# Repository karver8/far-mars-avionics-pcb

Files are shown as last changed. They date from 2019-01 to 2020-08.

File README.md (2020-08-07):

# far-mars-avionics-controller

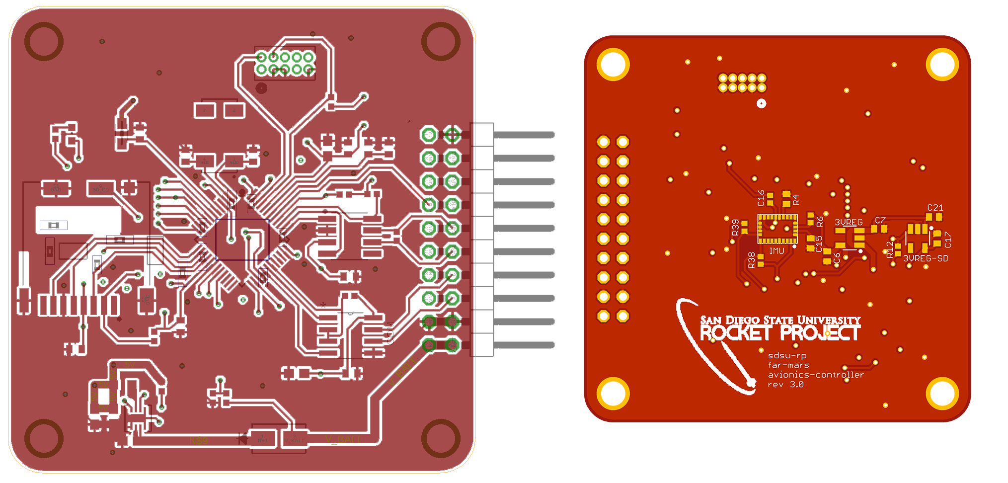
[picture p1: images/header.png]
PCB Layout Graphic


The **far-mars-avionics-controller** is a custom built printed circuit board that performs data aquisition, logging, and communication, all in one highly power effecient, light weight, and compact design. This circuit was built around the FAR/MARS rocket competition, which challenges teams to design a LOX/Methane rocket to accuratley target an altitude of 45,000 feet.

### Features
* Dual(5V/3.3V) Supply ARM Cortex M0+ microcontroller
* 9 multi-purpose 5V I/O pins (+1 DIO PIN)
* Up to 9 12bit and 2 16bit Analog to Digital channels.
* RS-485 Transceiver for long distance LVDS ground communications
* CANbus Transceiver for future feature expansion(untested)
* BNO055 Inertial Measurement Unit
* Locking microSD card slot for secure, vibration resistant data logging
* 5-17V Input Range allowing for versatile power supply.
* Power Effecient enabling the use of a tiny battery
* Very light, weighs less than an ounce!
* Built-in battery charge monitoring.
* Highly accurate crystal for detailed timestamping.

### Firmware

The FAR/MARS rocket uses a FreeRTOS implementation to safley and predictabley manage the various avionics tasks required to launch the rocket. Documentation and development of the firmware for this board can be found in our [far-mars-onboard-firmware](https://github.com/SDSURocketProject/far-mars-onboard-firmware) repository. 

### Documentation
Here is everything you need to interface with this PCB and/or to write your own drivers and firmware:
* [Pinout](/documentation/pinout.pdf "Pinout")
* [Schematic](/documentation/schematic.pdf "Schematic")
* [Mechanical Drawing](/documentation/mech_drawing.pdf "Drawing")
* [Device Datasheet Collection](/documentation/Datasheets "Device Datasheet Collection")

### Assembly
It is highly recommend that you outsource the assembly of this PCB. This design has a lot of tiny surface mount components, on both sides of the board, so unless you have experience reflowing on two sides, this will be almost impossible to assemble yourself. We used MacroFab for the most recent version of this PCB. The current BOM is also optimized to take advantage of their 10-day turnaround service. Here is everything you need to assemble your own avionics controller:
* [Assembly Guide](/assembly#assembly-guide "Instructions")
* [Bill of Materials](/assembly/BOM#bill-of-materials "Bill of Materials")
* [Gerber Files](/assembly/Gerbers)
* [Design Slides](/assembly/Physical%20Summary.pdf "Physical Summary")
* **Schematic & Layout Files are in the top directory**

### Remarks
The far-mars-avionics-controller is entirley functional and usable on any system with similar requirements to the FAR/MARS Lady Elizabeth rocket. Furthermore the CANbus port included in the design, once tested, will also allow for the PCB to interface with virtually any existing CANbus compatible product/system(e.g. Motor Controllers, Thermocouple modules). 

That all said the main purpose of this project was to demonstrate SDSU Rocket Projects ability to design highly purpose built custom electronics, and it was specifically designed around the rules specified by the FAR/MARS rocket competition. This PCB is far from being an all in one solution to any Avionics requirments you may have. The design may find most of its value as a supplement to a larger system.

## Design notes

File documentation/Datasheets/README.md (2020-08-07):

### Datasheet Index
* [Atmel SAMC21G ARM Cortex M0](/documentation/Datasheets/atmel-samc21datasheet.pdf "Atmel SAMC21G ARM Cortex M0+")
* [BNO055 Inertial Measurment Unit](/documentation/Datasheets/BST-BNO055-DS000.pdf "BNO055 Inertial Measurment Unit")
* [SanDisk microSD](/documentation/Datasheets/sandisk-microSD.pdf "SanDisk microSD")
* [microSD Slot Mechanical Specs](/documentation/Datasheets/microSD_DM3_catalog.pdf "microSD Slot Mechanical Specs")
* [RS485 Transceiver](/documentation/Datasheets/sn65hvd35.pdf "RS485 Transciever ")
* [CAN Transceiver](/documentation/Datasheets/MCP2561T.pdf)
* [5V DC/DC Switching Regulator](/documentation/Datasheets/tps62161.pdf)
* [3.3V Linear Regulator](/documentation/Datasheets/tlv702.pdf)
* [Reverse Protection Diode](/documentation/Datasheets/ds13002.pdf)
* [Tuning Fork Crystal](/documentation/Datasheets/abs25.pdf)

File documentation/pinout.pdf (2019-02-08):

# FAR/MARS AVIONICS PINOUT

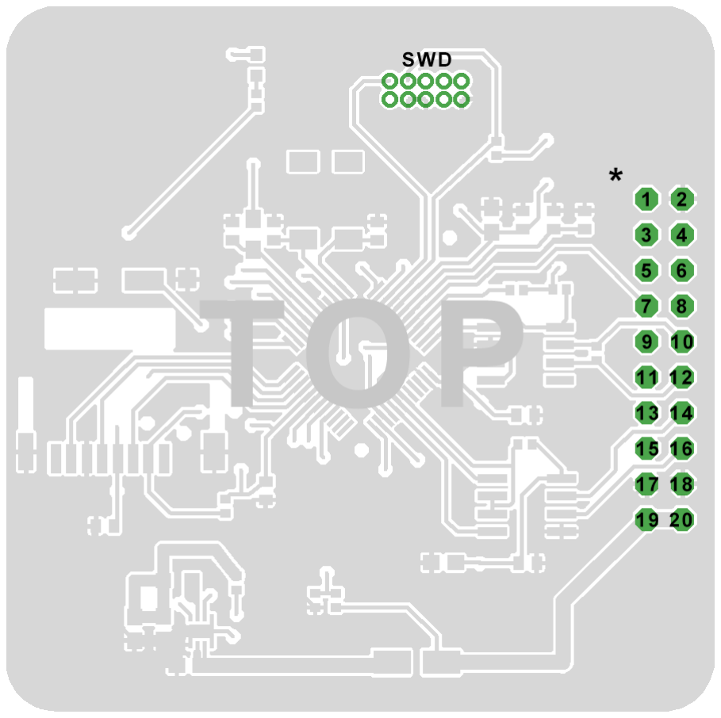
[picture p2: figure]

FULL PIN FUNCTION FOUND ON SAMC21G "I/O Multiplexing & Considerations", pg. 30 of Datasheet
Physical PIN # | Primary Function | SAMC21 PIN # | Supply | ADC | SD-ADC(16-bit) | PWM | SERCOM A | MISC
1 | 5V | -
2 | GND | -
3 | Multi-Function I/O | PB02 | 5V | AIN10 | | | SER5:0
4 | Multi-Function I/O | PB03 | 5V | AIN11 | | | SER5:1
5 | Multi-Function I/O | PA02 | 5V | AIN0 | | | | DAC
6 | Multi-Function I/O | PB08 | 5V | AIN2 | SDADC1:N | TC4:0 | SER4:0
7 | Digital I/O | PA28 | 5V
8 | Multi-Function I/O | PB09 | 5V | AIN3 | SDADC1:P | TC4:1 | SER4:1
9 | Multi-Function I/O | PA04 | 5V | AIN4 | | TC0:0 | SER0:0 | REFB
10 | CAN H | -
11 | Multi-Function I/O | PA05 | 5V | AIN5 | | TC0:1 | SER0:1
12 | CAN L | -
13 | Multi-Function I/O | PA06 | 5V | AIN6 | SDADC0:N | TC1:0 | SER0:2
14 | RS485 B | -
15 | Multi-Function I/O | PA07 | 5V | AIN7 | SDADC0:P | TC1:1 | SER0:3
16 | RS485 A | -
17 | GND | -
18 | GND | -
19 | VIN/BATT | -
20 | VIN/BATT | -

### Lady Elizabeth Specific

Physical PIN # | Primary Function | SAMC21 PIN # | Supply | Static Hot Fire | Launch | Description
1 | 5V | - | | UNUSED | UNUSED
2 | GND | - | | UNUSED | UNUSED
3 | 12 bit ADC | PB02 | 5V | TBD | UNUSED | TBD
4 | 12 bit ADC | PB03 | 5V | TBD | UNUSED | TBD
5 | 12 bit ADC | PA02 | 5V | Liquid Methane Tank PT | Liquid Methane Tank PT | 1500PSI 0.5-4.5V Analog PT
6 | 12 bit ADC | PB08 | 5V | Liquid Oxygen Tank PT | Liquid Oxygen Tank PT | 1500PSI 0.5-4.5V Analog PT
7 | Digital I/O | PA28 | 5V | UNUSED | UNUSED
8 | 16 bit SDADC | PB09 | 5V | Helium Tank PT | Helium Tank PT | 5800PSI 0-5V Analog PT
9 | Multi-Function I/O | PA04 | 5V | UNUSED | UNUSED
10 | CAN H | - | | UNUSED | UNUSED
11 | Multi-Function I/O | PA05 | 5V | UNUSED | UNUSED
12 | CAN L | - | | UNUSED | UNUSED
13 | 12 bit ADC | PA06 | 5V | TBD | UNUSED | TBD
14 | RS485 B | - | | Ground Coms | Ground Coms | Up to 1500m, Half-Duplex
15 | 16 bit SDADC | PA07 | 5V | Chamber Pressure PT | Chamber Pressure PT | TBD
16 | RS485 A | - | | Ground Coms | Ground Coms | Up to 1500m, Half-Duplex
17 | GND | - | | Ducer GND | Ducer GND | Ducer GND
18 | GND | - | | 11.1V 3S LiPo Ground | 11.1V 3S LiPo Ground | 11.1V 3S LiPo Ground
19 | VIN/BATT | - | | Ducer VOUT | Ducer VOUT | Ducer VOUT
20 | VIN/BATT | - | | 11.1V 3S LiPo Power In | 11.1V 3S LiPo Power In | 11.1V 3S LiPo Power In

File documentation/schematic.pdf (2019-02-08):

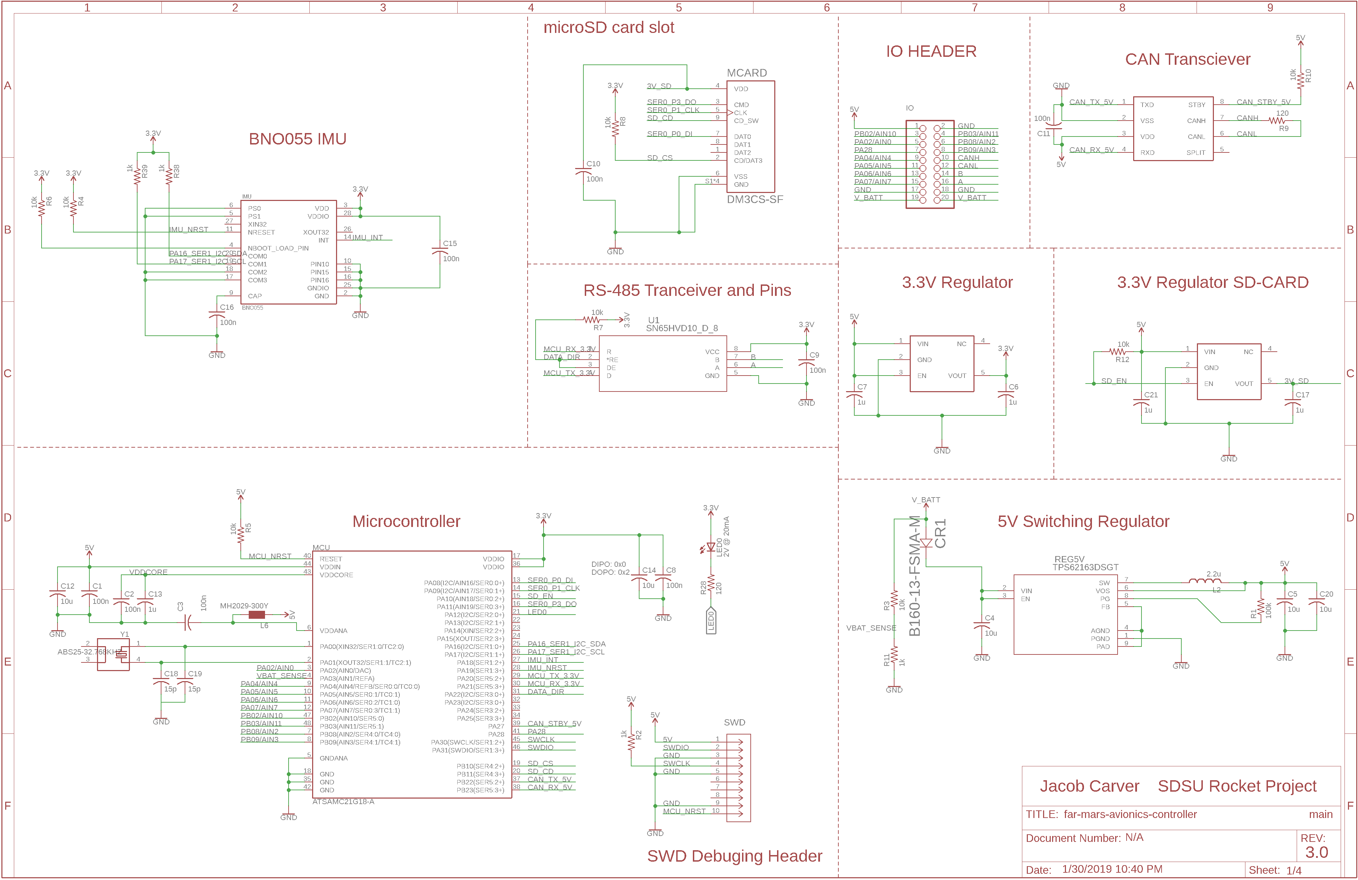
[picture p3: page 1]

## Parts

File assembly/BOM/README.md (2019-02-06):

## Bill of Materials

Here are two lists of materials you will need to both assemble and interface with the board.

* [Materials for PCB Assembly](https://github.com/SDSURocketProject/far-mars-avionics-pcb/blob/master/assembly/BOM/Onboard-BOM.csv)
* [Other Required Items](https://github.com/SDSURocketProject/far-mars-avionics-pcb/blob/master/assembly/BOM/OffBoard-BOM.csv)

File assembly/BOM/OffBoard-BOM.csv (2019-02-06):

Component/Part Name | Part Number | Link | Description | Vendor
Atmel ICE Debugger | ATATMEL-ICE-ND | https://www.digikey.com/product-detail/en/microchip-technology/ATATMEL-ICE/ATATMEL-ICE-ND/4753379 | PROGRAMMER FOR SAM | Digikey
Female Main Connector | A3DDH-2006G-ND | https://www.digikey.com/product-detail/en/te-connectivity-amp-connectors/A3DDH-2006G/A3DDH-2006G-ND/826121 | IDC CABLE - AKR20H/AE20G/AKR20H | Digikey
RS485 FTDI Wire End | USB-RS485-WE-1800-BT-FTDI_IT | https://www.amazon.com/FTDI-USB-RS485-WE-1800-BT-CABLE-RS485-SERIAL/dp/B00DK85QY4?s=electronics | RS485 to USB FTDI Adapter | Amazon
5-17V Power Source | N/A | N/A | N/A | Any

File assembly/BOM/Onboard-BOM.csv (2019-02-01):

Component/Part Name | Part Number | Link | Description | Vendor | MacroFab House Part | Qty Per Brd
ARM® Cortex®-M0+ SAM C21 | ATSAMC21G18A-AUTCT-ND | https://www.digikey.com/product-detail/en/microchip-technology/ATSAMC21G18A-AUT/ATSAMC21G18A-AUTCT-ND/5876003 | IC MCU 32BIT 256KB FLASH 48TQFP | Digikey |  | 1
10 (8 + 2) Position microSD Card Connector | HR1972CT-ND | https://www.digikey.com/product-detail/en/hirose-electric-co-ltd/DM3CS-SF/HR1972CT-ND/2602740 | CONN MICRO SD CARD HINGED TYPE | Digikey |  | 1
Red 633nm LED | 475-2512-1-ND | https://www.digikey.com/product-detail/en/osram-opto-semiconductors-inc/LS-Q976-NR-1/475-2512-1-ND/1802639 | LED RED DIFFUSED 0603 SMD | Digikey |  | 1
Ferrite Bead Filter | MH2029-300YCT-ND | https://www.digikey.com/product-detail/en/bourns-inc/MH2029-300Y/MH2029-300YCT-ND/3741761 | FERRITE BEAD 30 OHM 0805 1LN | Digikey |  | 1
2.2µH Unshielded Wirewound Inductor | 587-2064-1-ND | https://www.digikey.com/product-detail/en/taiyo-yuden/BRL2012T2R2M/587-2064-1-ND/1789011 | FIXED IND 2.2UH 550MA 390 MOHM | Digikey |  | 1
Right Angle 20 position Main Header | A97487-ND | https://www.digikey.com/product-detail/en/te-connectivity-amp-connectors/5103311-5/A97487-ND/1596774 | CONN HEADER R/A 20POS 2.54MM | Digikey |  | 1
BNO055 Inertial Measurment Unit | 828-1058-1-ND | https://www.digikey.com/product-detail/en/bosch-sensortec/BNO055/828-1058-1-ND/6136309 | IMU ACCEL/GYRO/MAG I2C 28LGA | Digikey |  | 1
Diode Schottky Reverse Voltage Protection | B140-FDICT-ND | https://www.digikey.com/product-detail/en/diodes-incorporated/B140-13-F/B140-FDICT-ND/815319 | DIODE SCHOTTKY 40V 1A SMA | Digikey | Yes | 1
10µF Ceramic Capacitor | 445-9065-1-ND | https://www.digikey.com/product-detail/en/tdk-corporation/C1608X5R1C106M080AB/445-9065-1-ND/3648729 | CAP CER 10UF 16V X5R 0603 | Digikey | Yes | 5
0.1µF Ceramic Capacitor | 490-3261-1-ND | https://www.digikey.com/product-detail/en/murata-electronics-north-america/GRM155R71C104KA88D/490-3261-1-ND/702802 | CAP CER 0.1UF 16V X7R 0402 | Digikey | Yes | 9
3.3V Linear Voltage Regulator | 296-32415-1-ND | https://www.digikey.com/product-detail/en/texas-instruments/TLV70233DBVR/296-32415-1-ND/3505572 | IC REG LINEAR 3.3V 300MA SOT23-5 | Digikey | Yes | 2
1µF Ceramic Capacitor | 445-4978-1-ND | https://www.digikey.com/product-detail/en/tdk-corporation/C1005X5R1C105K050BC/445-4978-1-ND/2093592 | CAP CER 1UF 16V X5R 0402 | Digikey | Yes | 5
15pF Capacitor for Crystal | 478-1072-1-ND | https://www.digikey.com/product-detail/en/avx-corporation/04025A150JAT2A/478-1072-1-ND/564104 | CAP CER 15PF 50V C0G/NP0 0402 | Digikey |  | 2
CANbus Transciever | MCP2561T-E/SNCT-ND | https://www.digikey.com/product-detail/en/microchip-technology/MCP2561T-E-SN/MCP2561T-E-SNCT-ND/5148846 | IC TXRX CAN 8SOIC | Digikey |  | 1
10k Chip Resistor | P10KJCT-ND | https://www.digikey.com/product-detail/en/microchip-technology/MCP2561T-E-SN/MCP2561T-E-SNCT-ND/5148846 | RES SMD 10K OHM 5% 1/10W 0402 | Digikey | Yes | 8
1k Chip Resistor | P1.0KJCT-ND | https://www.digikey.com/product-detail/en/panasonic-electronic-components/ERJ-2GEJ102X/P1.0KJCT-ND/146897 | RES SMD 1K OHM 5% 1/10W 0402 | Digikey | Yes | 4
100k Chip Resistor | P100KJCT-ND | https://www.digikey.com/product-detail/en/panasonic-electronic-components/ERJ-2GEJ104X/P100KJCT-ND/146730 | RES SMD 100K OHM 5% 1/10W 0402 | Digikey | Yes | 1
CAN Termination Resistor | ERJ-S02F1200X-ND | https://www.digikey.com/product-detail/en/panasonic-electronic-components/ERJ-S02F1200X/ERJ-S02F1200X-ND/672934 | RES SMD 120 OHM 1% 1/10W 0402 | Digikey |  | 2
5V Switch Regulator | 296-30228-1-ND | https://www.digikey.com/product-detail/en/texas-instruments/TPS62163DSGT/296-30228-1-ND/2982147 | IC REG BUCK 5V 1A SYNC 8WSON | Digikey |  | 1
SWD Header | 609-3712-ND | https://www.digikey.com/product-detail/en/amphenol-icc-fci/20021111-00010T4LF/609-3712-ND/2209072 | CONN HEADER VERT 10POS 1.27MM | Digikey |  | 1
RS485 Transciever | 296-24734-1-ND | https://www.digikey.com/product-detail/en/texas-instruments/SN65HVD10MDREP/296-24734-1-ND/2092556 | IC TXRX RS485 EP 3.3V 8SOIC | Digikey |  | 1
32.768kHz ±10ppm Crystal | 535-9809-1-ND | https://www.digikey.com/product-detail/en/abracon-llc/ABS25-32.768KHZ-1-T/535-9809-1-ND/2001432 | CRYSTAL 32.7680KHZ 12.5PF SMD | Digikey |  | 1

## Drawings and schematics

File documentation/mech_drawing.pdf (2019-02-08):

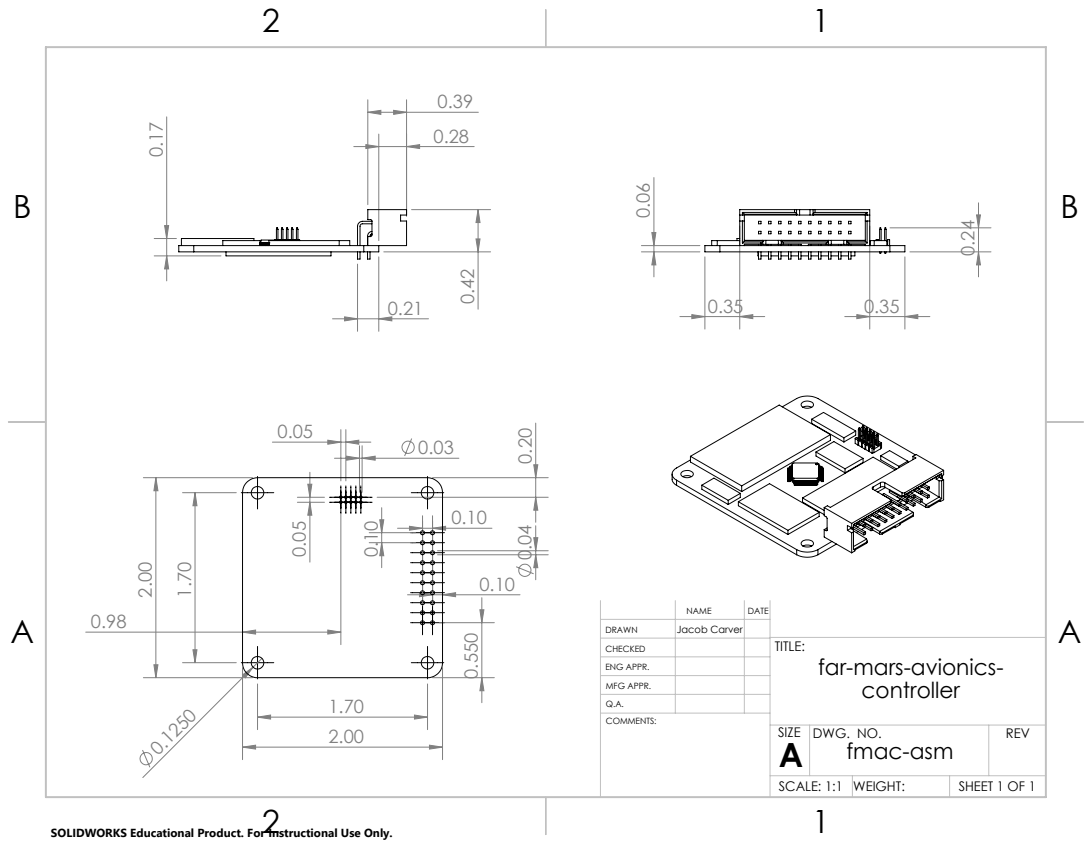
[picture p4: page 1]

DRAWN | Jacob Carver
CHECKED | | TITLE: far-mars-avionics-controller

ENG APPR.
MFG APPR.
Q.A.

SIZE A | DWG. NO. fmac-asm | REV

SCALE: 1:1 | WEIGHT: | SHEET 1 OF 1

SOLIDWORKS Educational Product. For Instructional Use Only.

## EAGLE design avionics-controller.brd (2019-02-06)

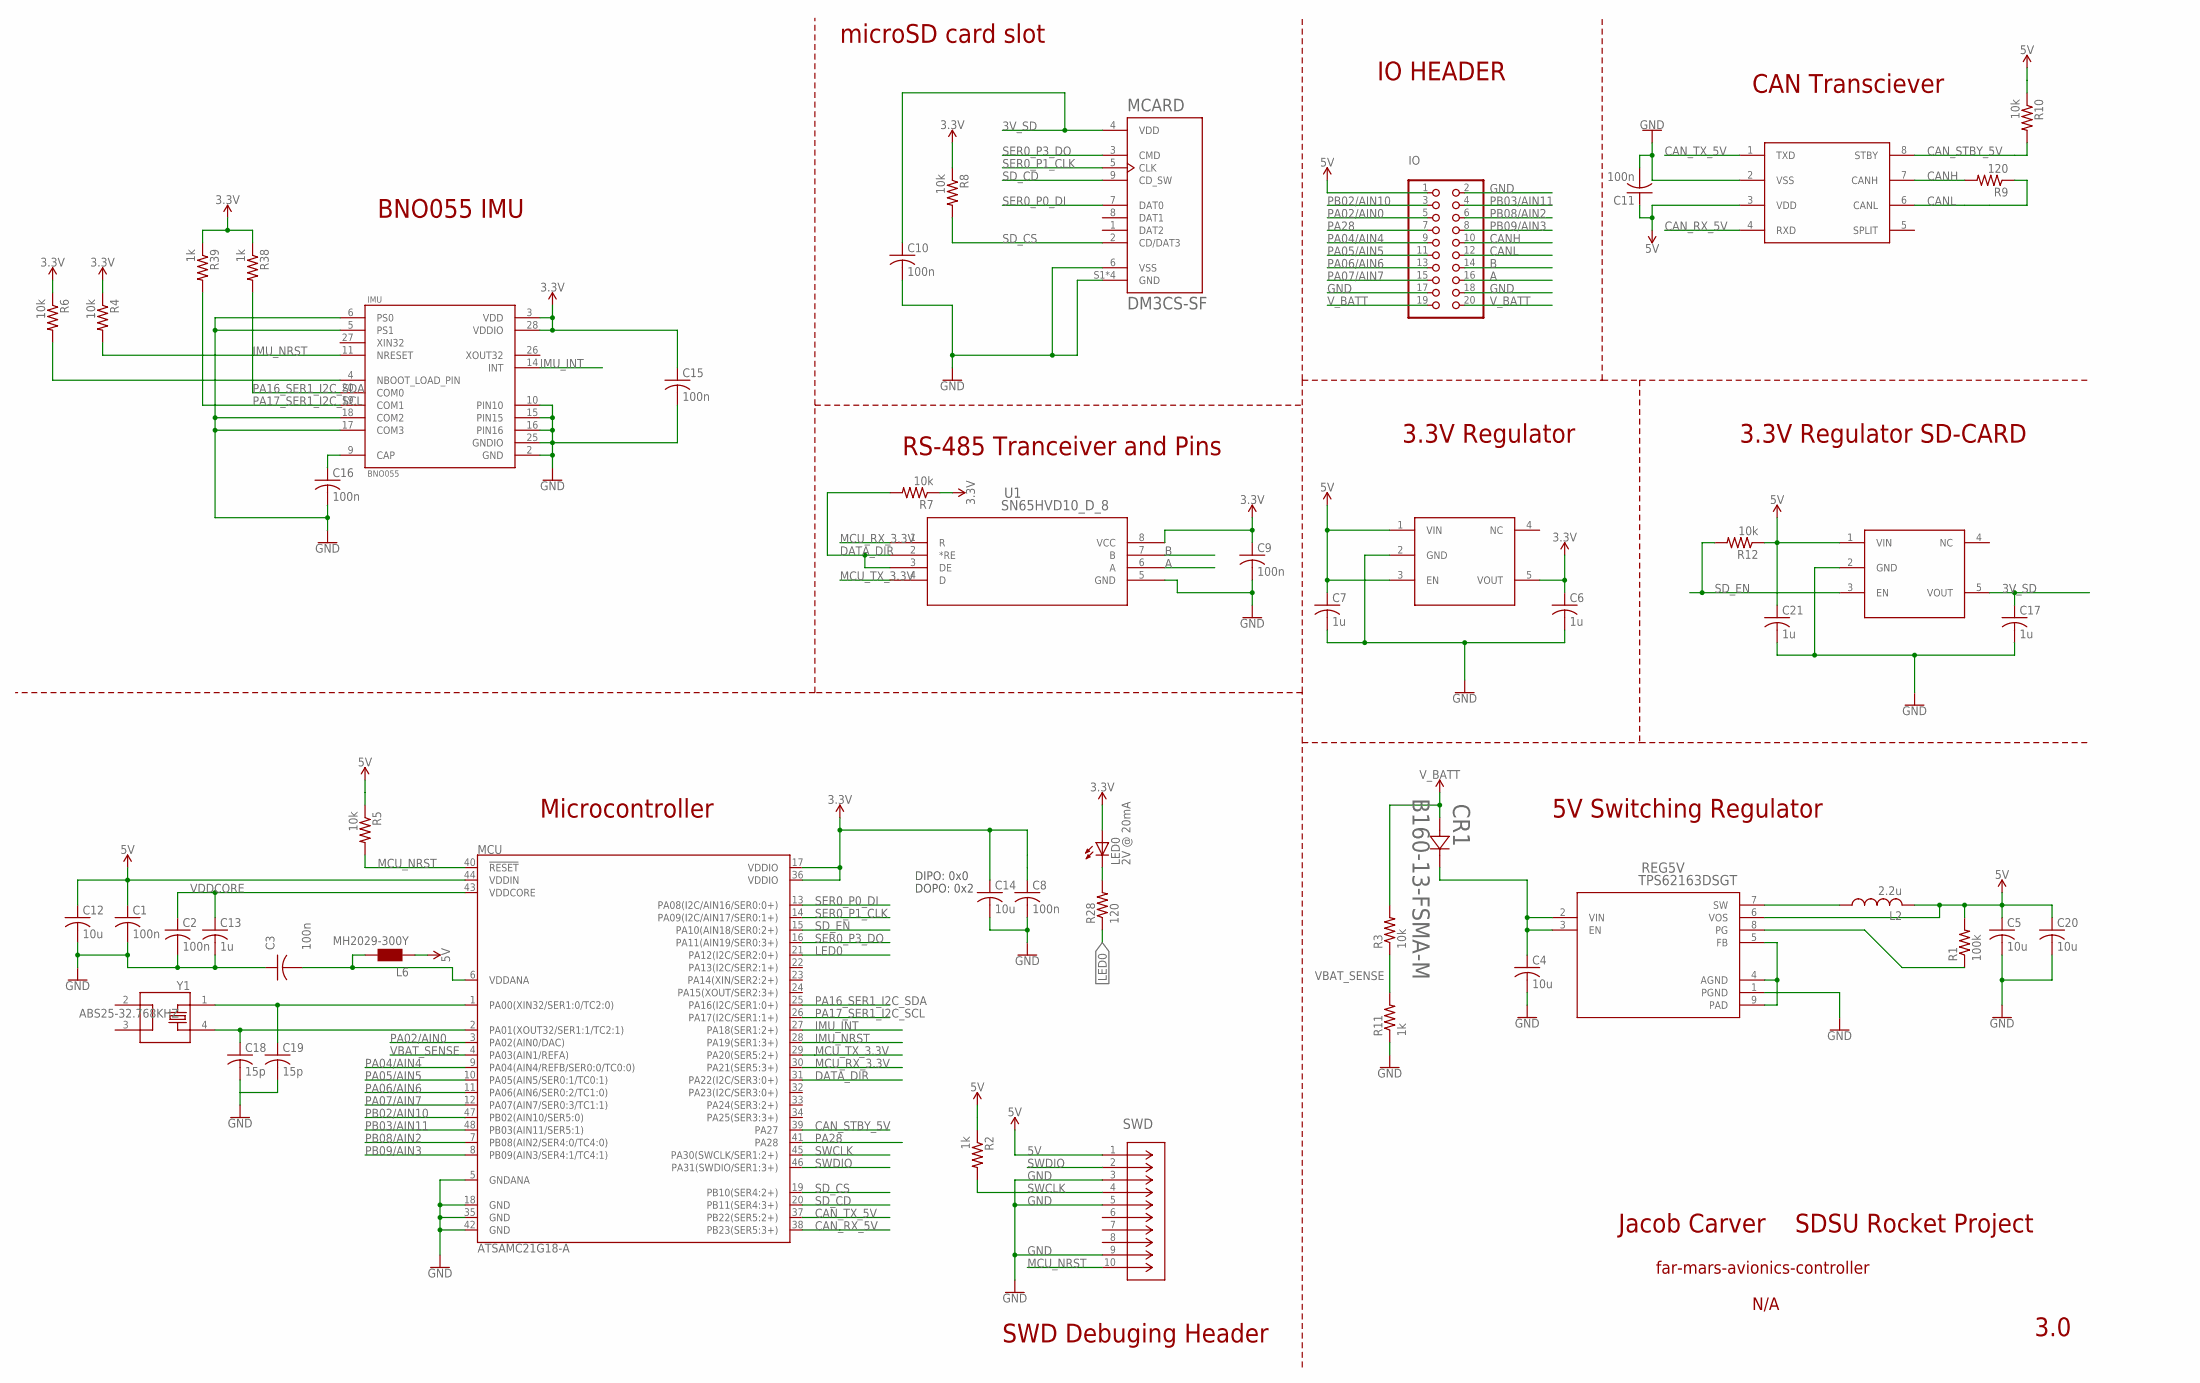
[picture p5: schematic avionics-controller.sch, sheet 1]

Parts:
3VREG, 3VREG-SD: 3.3VREGULATOR; SOT95P280X110-5
C1, C2, C3, C8, C9, C10, C11, C15, C16: 100n; C0402
C4, C5, C12, C14, C20: 10u; C0603
C6, C7, C13, C17, C21: 1u; C0402
C18, C19: 15p; C0402
CAN: MCP2561T-E8SOIC; SOIC127P600X175-8
CR1: B160-13-FSMA-M; SMA-M
IMU: BNO055; LGA28R50P4X10_380X520X100
IO: PINHD-2X10/90; 2X10/90
L2: 2.2u; L2012C
L6: MH2029-300Y; 0805
LED0: 2V @ 20mA; CHIPLED_0603
MCARD: DM3CS-SF; HRS_DM3CS-SF
MCU: ATSAMC21G18-A; TQFP-48
R1: 100k; R0402
R2, R11, R38, R39: 1k; R0402
R3, R4, R5, R6, R7, R8, R10, R12: 10k; R0402
R9, R28: 120; R0402
REG5V: TPS62163DSGT; DSG8_1P6X0P9
SWD: DEBUG-HEADER; CONN_MINITEK_2X5_HDR
U1: SN65HVD10_D_8; D8
Y1: ABS25-32.768KHZ; ABS25-32.768KHZ-6-T

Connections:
3.3V: 3VREG.5 (VOUT), C6.1, C8.1, C9.1, C14.1, C15.1, IMU.3 (VDD), IMU.28 (VDDIO), LED0.A, MCU.17 (VDDIO), MCU.36 (VDDIO), R4.1, R6.1, R7.1, R8.1, R38.1, R39.1, U1.8 (VCC)
3V_SD: 3VREG-SD.5 (VOUT), C10.1, C17.1, MCARD.4 (VDD)
5V: 3VREG.1 (VIN), 3VREG.3 (EN), 3VREG-SD.1 (VIN), C1.1, C5.1, C7.1, C11.1, C12.1, C20.1, C21.1, CAN.3 (VDD), IO.1, L2.2, L6.1, MCU.44 (VDDIN), R1.2, R2.1, R5.1, R10.1, R12.1, REG5V.6 (VOS), SWD.1
A: IO.16, U1.6 (A)
B: IO.14, U1.7 (B)
CANH: CAN.7 (CANH), IO.10, R9.2
CANL: CAN.6 (CANL), IO.12, R9.1
CAN_RX_5V: CAN.4 (RXD), MCU.38 (PB23(SER5:3+))
CAN_STBY_5V: CAN.8 (STBY), MCU.39 (PA27), R10.2
CAN_TX_5V: CAN.1 (TXD), MCU.37 (PB22(SER5:2+))
DATA_DIR: MCU.31 (PA22(I2C/SER3:0+)), R7.2, U1.2 (*RE), U1.3 (DE)
GND: 3VREG.2 (GND), 3VREG-SD.2 (GND), C1.2, C2.2, C3.1, C4.2, C5.2, C6.2, C7.2, C8.2, C9.2, C10.2, C11.2, C12.2, C13.2, C14.2, C15.2, C16.2, C17.2, C18.2, C19.2, C20.2, C21.2, CAN.2 (VSS), IMU.2 (GND), IMU.5 (PS1), IMU.6 (PS0), IMU.10 (PIN10), IMU.15 (PIN15), IMU.16 (PIN16), IMU.17 (COM3), IMU.18 (COM2), IMU.25 (GNDIO), IO.2, IO.17, IO.18, MCARD.6 (VSS), MCARD.S1 (GND), MCARD.S2 (GND), MCARD.S3 (GND), MCARD.S5 (GND), MCU.5 (GNDANA), MCU.18 (GND), MCU.35 (GND), MCU.42 (GND), R11.1, REG5V.1 (PGND), SWD.3, SWD.5, SWD.9, U1.5 (GND)
IMU_INT: IMU.14 (INT), MCU.27 (PA18(SER1:2+))
IMU_NRST: IMU.11 (NRESET), MCU.28 (PA19(SER1:3+)), R4.2
LED0: MCU.21 (PA12(I2C/SER2:0+)), R28.1
MCU_NRST: MCU.40 (!RESET!), R5.2, SWD.10
MCU_RX_3.3V: MCU.30 (PA21(SER5:3+)), U1.1 (R)
MCU_TX_3.3V: MCU.29 (PA20(SER5:2+)), U1.4 (D)
unnamed: R1.1, REG5V.8 (PG)
unnamed: C3.2, L6.2, MCU.6 (VDDANA)
unnamed: L2.1, REG5V.7 (SW)
unnamed: REG5V.4 (AGND), REG5V.5 (FB), REG5V.9 (PAD)
unnamed: C4.1, CR1.1 (12), REG5V.2 (VIN), REG5V.3 (EN)
unnamed: C19.1, MCU.1 (PA00(XIN32/SER1:0/TC2:0)), Y1.1
unnamed: C18.1, MCU.2 (PA01(XOUT32/SER1:1/TC2:1)), Y1.4
unnamed: C16.1, IMU.9 (CAP)
unnamed: IMU.4 (NBOOT_LOAD_PIN), R6.2
unnamed: LED0.C, R28.2
PA02/AIN0: IO.5, MCU.3 (PA02(AIN0/DAC))
PA04/AIN4: IO.9, MCU.9 (PA04(AIN4/REFB/SER0:0/TC0:0))
PA05/AIN5: IO.11, MCU.10 (PA05(AIN5/SER0:1/TC0:1))
PA06/AIN6: IO.13, MCU.11 (PA06(AIN6/SER0:2/TC1:0))
PA07/AIN7: IO.15, MCU.12 (PA07(AIN7/SER0:3/TC1:1))
PA16_SER1_I2C_SDA: IMU.20 (COM0), MCU.25 (PA16(I2C/SER1:0+)), R38.2
PA17_SER1_I2C_SCL: IMU.19 (COM1), MCU.26 (PA17(I2C/SER1:1+)), R39.2
PA28: IO.7, MCU.41 (PA28)
PB02/AIN10: IO.3, MCU.47 (PB02(AIN10/SER5:0))
PB03/AIN11: IO.4, MCU.48 (PB03(AIN11/SER5:1))
PB08/AIN2: IO.6, MCU.7 (PB08(AIN2/SER4:0/TC4:0))
PB09/AIN3: IO.8, MCU.8 (PB09(AIN3/SER4:1/TC4:1))
SD_CD: MCARD.9 (CD_SW), MCU.20 (PB11(SER4:3+))
SD_CS: MCARD.2 (CD/DAT3), MCU.19 (PB10(SER4:2+)), R8.2
SD_EN: 3VREG-SD.3 (EN), MCU.15 (PA10(AIN18/SER0:2+)), R12.2
SER0_P0_DI: MCARD.7 (DAT0), MCU.13 (PA08(I2C/AIN16/SER0:0+))
SER0_P1_CLK: MCARD.5 (CLK), MCU.14 (PA09(I2C/AIN17/SER0:1+))
SER0_P3_DO: MCARD.3 (CMD), MCU.16 (PA11(AIN19/SER0:3+))
SWCLK: MCU.45 (PA30(SWCLK/SER1:2+)), R2.2, SWD.4
SWDIO: MCU.46 (PA31(SWDIO/SER1:3+)), SWD.2
VBAT_SENSE: MCU.4 (PA03(AIN1/REFA)), R3.1, R11.2
VDDCORE: C2.1, C13.1, MCU.43 (VDDCORE)
V_BATT: CR1.2 (21), IO.19, IO.20, R3.2

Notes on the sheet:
DIPO: 0x0
DOPO: 0x2
RS-485 Tranceiver and Pins
SWD Debuging Header
microSD card slot
IO HEADER
3.3V Regulator
CAN Transciever
5V Switching Regulator
Microcontroller
BNO055 IMU
3.3V Regulator SD-CARD
3.0
Jacob Carver SDSU Rocket Project
N/A
far-mars-avionics-controller

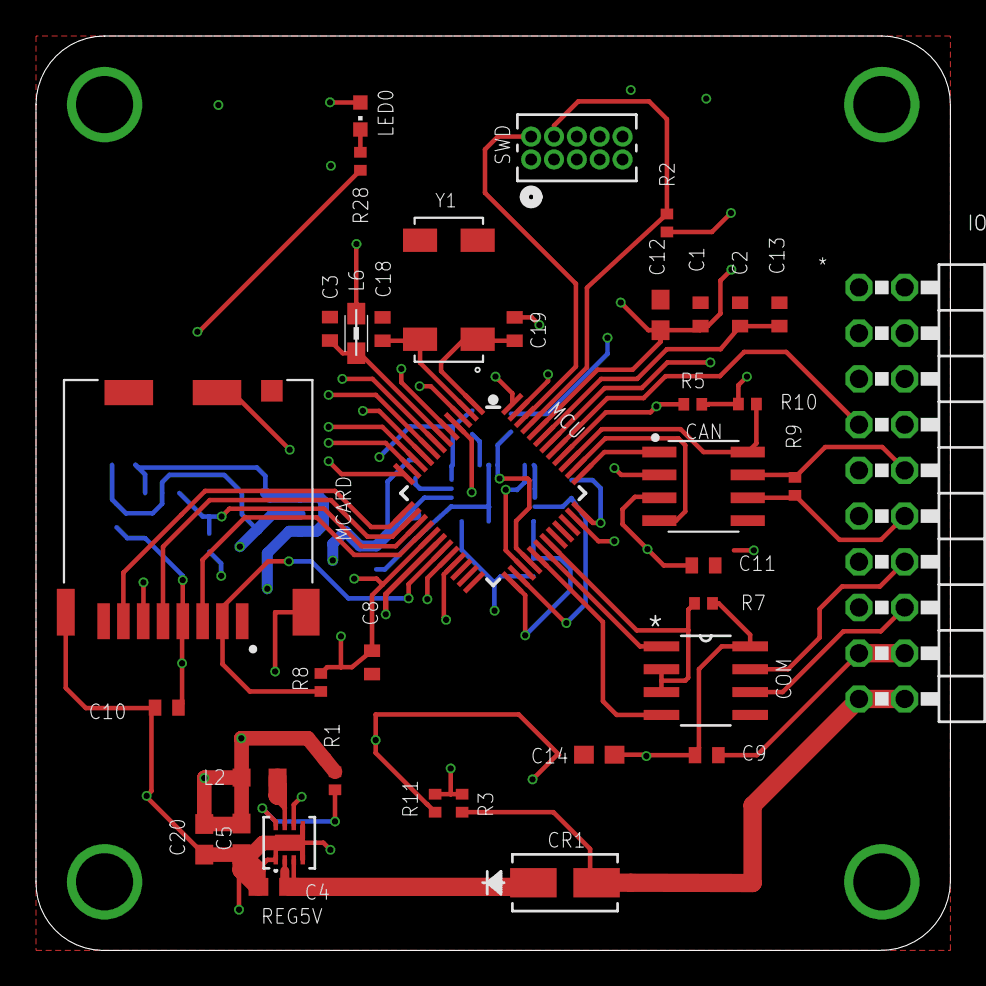
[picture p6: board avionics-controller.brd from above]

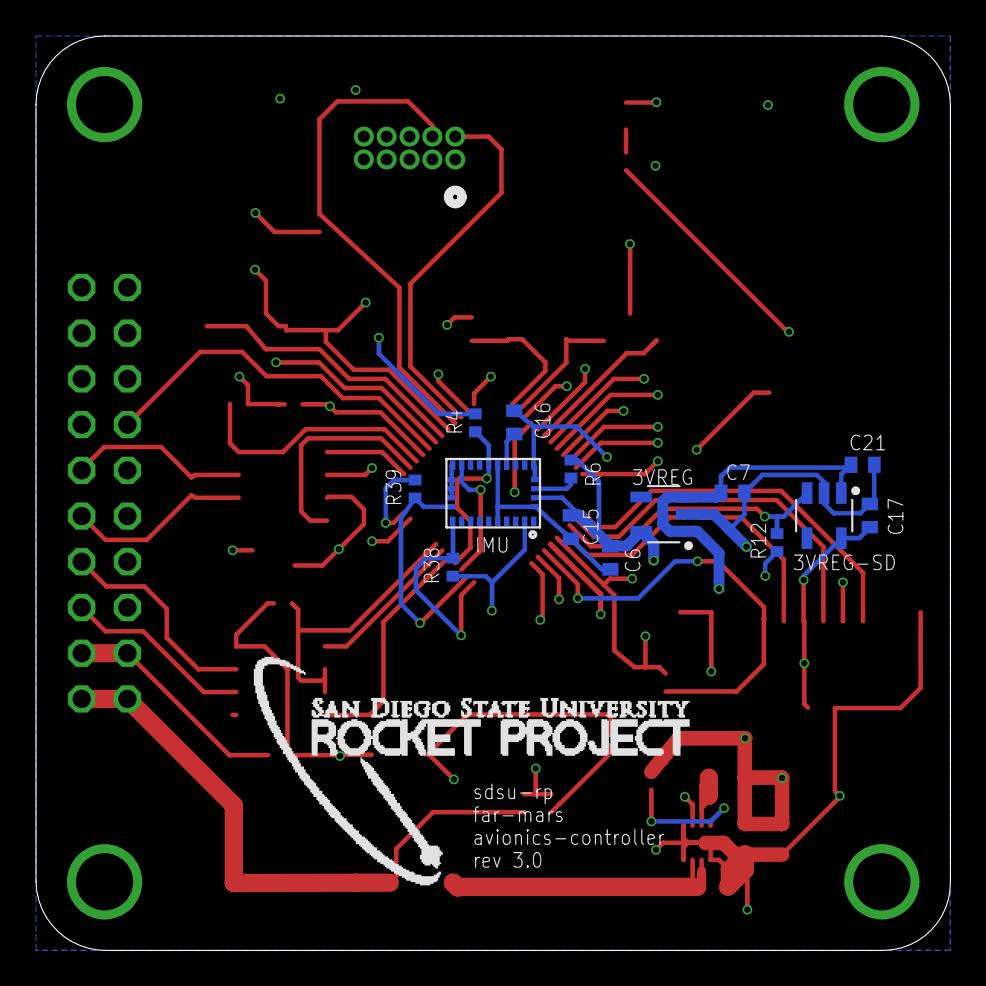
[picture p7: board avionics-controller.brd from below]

Board: 4 copper layers, 50.8 x 50.8 mm, 52 parts (15 on the bottom side), 51 nets.

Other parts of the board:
U$6: RP-LOGO

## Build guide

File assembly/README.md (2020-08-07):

# Assembly Guide
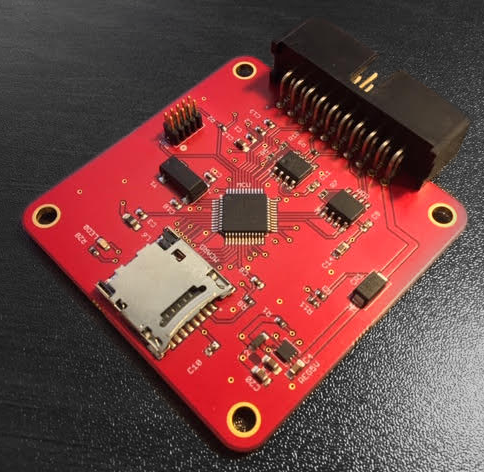
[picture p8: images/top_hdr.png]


If you are looking to acquire a far-mars-avionics-controller for yourself, here are the instructions you should follow. 

**Please contact [SDSU Rocket Project](https://www.sdsurocketproject.org/contact "SDSU Rocket Project") before assembling this PCB.**

The designers and organization take no responsibility over the use of any of the materials in this repository. 

### 0. Introduction
These directions are for ordering a PCB through [Macrofab](https://macrofab.com/ "Macrofab"), they were chosen for their ability to handle double sided reflow, LGA and BGA, their 10-day turn around service, warranty, and their nice UI. Pay me MacroFab. As of writing this, the entire order without shipping amounts to 160 USD, assembling this PCB yourself would be considerably cheaper, but if you are able to reflow two sides at once then you do not need this guide.

### 1. Setup
You will need to first make a [Macrofab](https://macrofab.com/ "Macrofab") account. Next download this repository to make it easier to drag and drop files into Macrofabs board wizard.

### 2. Start new PCB Wizard
Navigate to "PCBs" on the Macrofab website, and click on the "Create New PCB" button to start the wizard.

### 3. Upload your PCB
Navigate to [far-mars-avionics-pcb/assembly/Gerbers/](/assembly/Gerbers "far-mars-avionics-pcb/assembly/Gerbers/"). Gerber files are CAM and Drill instructions the fab house uses to make the PCB. Drag and Drop every file in this directory onto their wizard where it indicates, IGNORE everything in the CAMOutputs folder. You can also use the Eagle CAD .brd file located in this repository, there is no difference.

### 4. Populate the Bill Of Materials
This is somewhat tedious, so until I decide to figure out how to upload a premade BOM to their website, you will need to go through the the BOM in this repo and manually add each part. Navigate to [far-mars-avionics-pcb/assembly/BOM/Onboard-BOM.csv](/assembly/BOM/Onboard-BOM.csv "far-mars-avionics-pcb/assembly/BOM/Onboard-BOM.csv") and start adding everything you see there.

Note that the far right column indicates whether the parts are stocked by Macrofab, these reduce the cost of the board. Make sure to use their parts for these items, you can find the model number for these parts on their website under the House Parts tab.

It is highly likley that some of these parts will no longer be in stock, or no longer produced, so if this happens you will need to navigate Digikey or one of their approved suppliers to find a matching alternative.

### 5. 10-day Turnaround Optimization
Their 10-day turn around services requires that you use fewer than 20 unique parts and no PTH(Throughhole) parts. The one disadvantage of using the 10-day service for this PCB is that you will void the warranty soldering on the headers. If you are time starved or do not care, proceed, if not still remember to DNP(Do not place) the Rocket Project Logo, this is a glitch. 

You will notice that on the far right there are check boxes that say "DNP", this tells Macrofab not to source and assemble that specific part, in case you would like to do it yourself. For the 10-day service, DNP the "SWD" and "20 pin Main Header". Also as said above, DNP the RP Logo that appears on the BOM for whatever reason. You will need to order the parts you DNP so you can add them yourself.

Please note that the 10-day turnaround time is defined as 10 buisness days, not including weekends, the true turn around time is estimated in the top right of the wizard under where it should now say "10-days". **This does not include shipping time**.

### 6. Order Required Components
In [far-mars-avionics-pcb/assembly/BOM/OffBoard-BOM.csv](/assembly/BOM/OffBoard-BOM.csv "far-mars-avionics-pcb/assembly/BOM/OffBoard-BOM.csv") you will find a short list of things you will need to order outside of MacroFab. You need these in order to communicate, power, and flash/program it. If I missed something you feel should be on this list please let me know.

**Make sure to order any parts you DNP in step 5!**

### 7. Once you get the PCB
If you plan on using the firmware we wrote, located in a seperate [repository](https://github.com/SDSURocketProject/far-mars-onboard-firmware "repository"), you will need to get a little familiar with the Atmel-ICE programmer and Atmel Studio first. Once you've done this, you can hook up the ICE to the SWD header you will have soldered on by now, and flash the firmware onto the board. You will need to reference the firmwares documentation in order to adjust it to your needs.

If you would like to write your own firmware, you should use the firmware repository and Atmel Software Framwork as a guide. Embedded programming and RTOS knowledge are a must. These are very useful skills to have. 

### 8. Final Remarks
The far-mars-avionics-controller is entirley functional and usable on any system with similar requirements to the FAR/MARS Lady Elizabeth rocket. Furthermore the CANbus port included in the design, once tested, will also allow for the PCB to interface with virtually any existing CANbus compatible product/system(e.g. Motor Controllers, Thermocouple modules). 

That all said the main purpose of this project was to demonstrate SDSU Rocket Projects ability to design highly purpose built custom electronics, and it was specifically designed around the rules specified by the FAR/MARS rocket competition. This PCB is far from being an all in one solution to any Avionics requirments you may have. The design may find most of its value as a supplement to a larger system.

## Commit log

2018-02-09 Copied over from far-mars-onboard-pcb
    [main.brd, main.sch]
2018-02-09 First Layout and Schematic
    [main.brd, main.sch]
2018-02-09 Added some wires
    [main.brd]
2018-02-09 Added gnd pour
    [main.brd, main.sch]
2018-02-11 Added IMU
    [main.brd, main.sch]
2018-02-17 Schematic and Layout Optimizations
    Reconfigured a couple serial pins to make trace routing easier. Placed all compnents, just need to route and label.
    [main.brd, main.sch]
2018-02-17 Routed everything
    [main.brd, main.sch]
2018-02-17 Small tweaks before labels
    [main.brd, main.sch]
2018-02-17 Labeled compenents added logos
    [main.brd, main.sch]
2018-02-18 Some logo dpi fixes
    OSHpark wouldn't except a silkscreen above 400 dpi
    [main.brd]
2018-02-18 Added board renderings for readme
2018-02-18 Updated bom
2018-02-18 Added links to BOM
2018-02-18 Small switch adjustment, and render update for this change
    [main.brd, main.sch]
2018-02-19 Added headers and housings table to readme
2018-02-19 Organized Schematic
    Added borders, boxes, and labels
    [main.sch]
2018-02-19 Added schematic image capture
2018-02-20 Layout overview
    [main.brd]
2018-02-20 Fixed poly fill not connecting to all pins
    [main.brd]
2018-02-23 Changed coms transceiver, and updated documentation
    Also updated bill of materials
    [main.brd, main.sch]
2018-04-15 Switched out SWD header for one with bigger drills
    [main.brd, main.sch]
2018-06-09 Added some traces, added a reset signal to IMU
    [main.brd, main.sch]
2018-06-10 Added Higned SD, rearranged silk
    Added new hinged MicroSD for stability purposes, this sd card will be operating in a high g, high vibration enviornment and a spring ejection slot is not adequate. I also rearranged the labels on the silk screen as the headers were blocking a few. The SD card is also seated closer to the center, hopefully so the card no loner sticks out past the board dimensions.
    [main.brd, main.sch]
2018-06-12 Update microSD in bom to match new footprint in eagle files
2019-01-31 intial rev 3.0 update
    Initial files and structure of core documentation for rev 3.0 of the far-mars avionics computer. Will be updating and adding documents soon.
    [avionics-controller.brd, avionics-controller.sch, main.brd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]
2019-02-01 Added Documentation and BOM
    Added some IC datasheets and updated a few readmes to display bom and added CSV for bom
    [BOM.csv]
2019-02-06 Updated documentation(pinout, bom) and made small layout adjustment
    Added another BOM, updated BOM readme to remove markdown table and replaced with links, fixed small layout error that caused sd card to short GND to filters 5V pad when fully open. Added more datasheets.
    [OffBoard-BOM.csv, Onboard-BOM.csv, avionics-controller.brd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]
2019-02-06 Added Gerbers and Datasheet Index
    [avionics-controller.GBL, avionics-controller.GBO, avionics-controller.GBP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]
2019-02-06 Minor edits on readmes, Added Assembly Guide
    [OffBoard-BOM.csv, pinout.csv]
2019-02-06 Update README.md
    Fixed assembly guide formatting
2019-02-08 Added updated Pinout, Mechanical Drawing, and Electrical Schematic PDFs
2019-02-08 Update README.md
    Fixed schematic pdf link in main readme
2019-04-04 add empty altium project
    [lady-elizabeth-obc.PrjPCB]
2019-04-05 Initial include of altium translation of OBC rev3
    [BRL2012T2R2M-2.PcbLib, avionics-controller.PcbDoc, avionics-controller.PrjPCB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]
2019-04-05 move altium files to new directory
    [BRL2012T2R2M-2.PcbLib, avionics-controller.PcbDoc, avionics-controller.PrjPCB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]

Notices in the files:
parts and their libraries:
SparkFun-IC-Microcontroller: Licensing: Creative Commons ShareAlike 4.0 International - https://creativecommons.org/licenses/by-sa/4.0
